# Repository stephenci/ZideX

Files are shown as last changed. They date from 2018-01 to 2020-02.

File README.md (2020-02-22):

# ZideX
Open source 3D printer with dual extrusion and independent X and Z axis
This is a slightly more complicated version of IDEX.
This is also a crane style printer modified to add rigidity to handle fast and rapid movement.

<a href="https://imgur.com/TapHjAb">source: imgur.com</a>

<a href="https://imgur.com/pBOmRLS">source: imgur.com</a>

<a href="https://imgur.com/aCJxu8N">source: imgur.com</a>

<a href="https://imgur.com/a5UugVb">source: imgur.com</a>

<a href="https://imgur.com/xPmkoOy">source: imgur.com</a>

https://youtu.be/PqQjZGIJ1rw

Mostly build documentation and discussion can be found here:
https://openbuilds.com/builds/zidex.5259/

See link below to explore the fully assembled printer in 3D
https://skfb.ly/6vxOx

Full model STEP file posted on Onshape
https://cad.onshape.com/documents/0a614a4674c34d17fad6ca34/w/c56dc46b54dffcec5b4223f7/e/2df415dc5961ccc9e1978c58

license:
CC - Attribution NonCommercial - Share Alike - CC BY NC SA

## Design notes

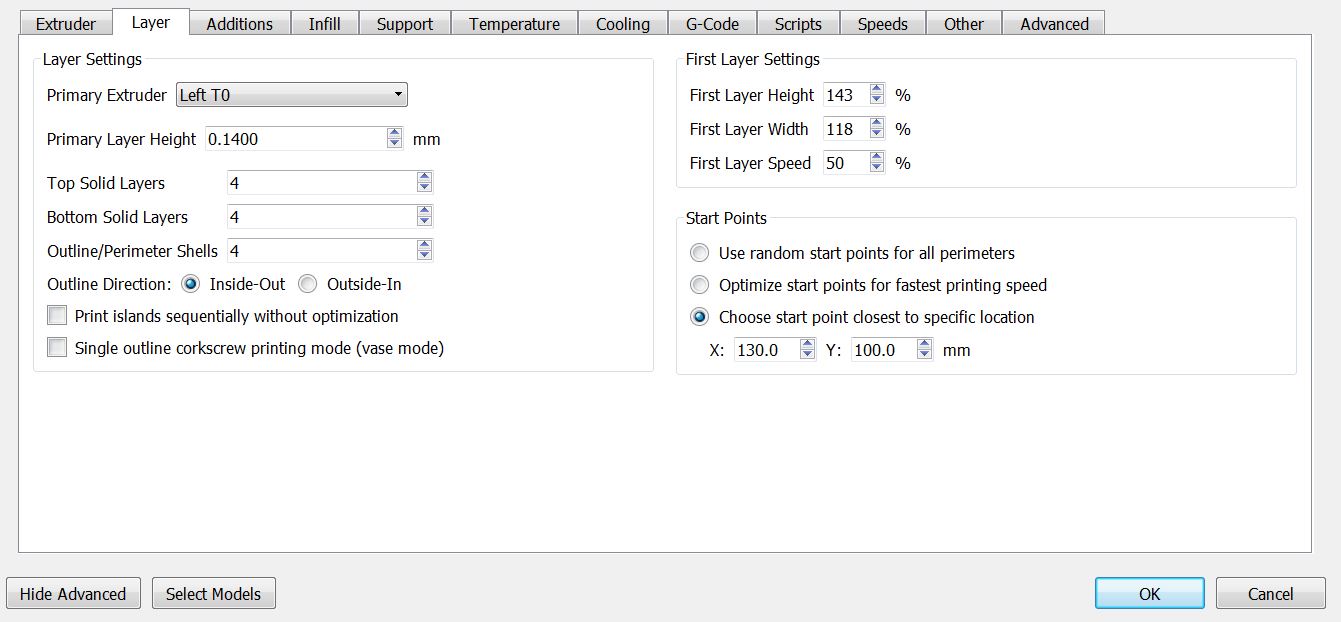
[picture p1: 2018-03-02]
Config/T0 setting (airbrush nozzle) - Layer.JPG

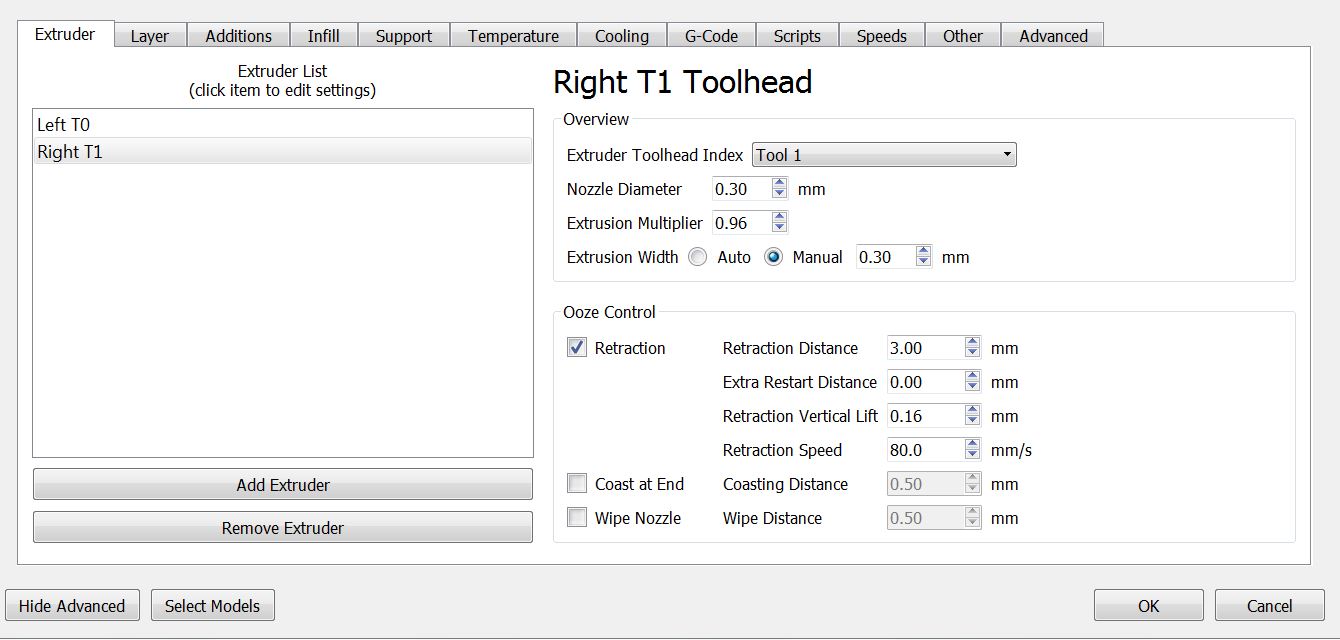
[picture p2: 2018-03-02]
Config/T1 setting (microswiss nozzle) - Extruder.JPG

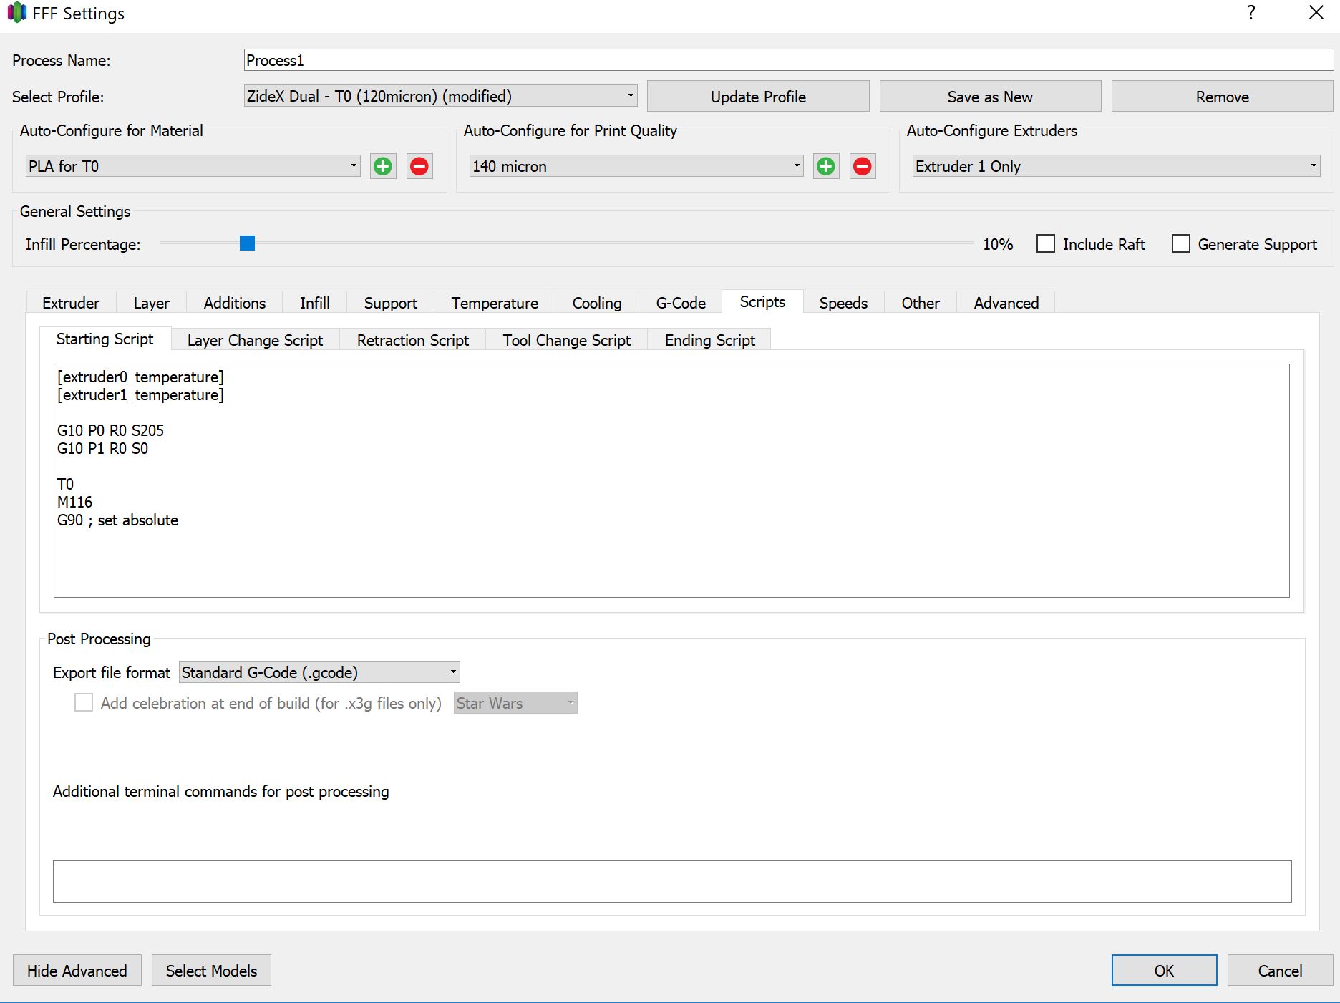
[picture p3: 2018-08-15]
Config/starting script S3D.JPG

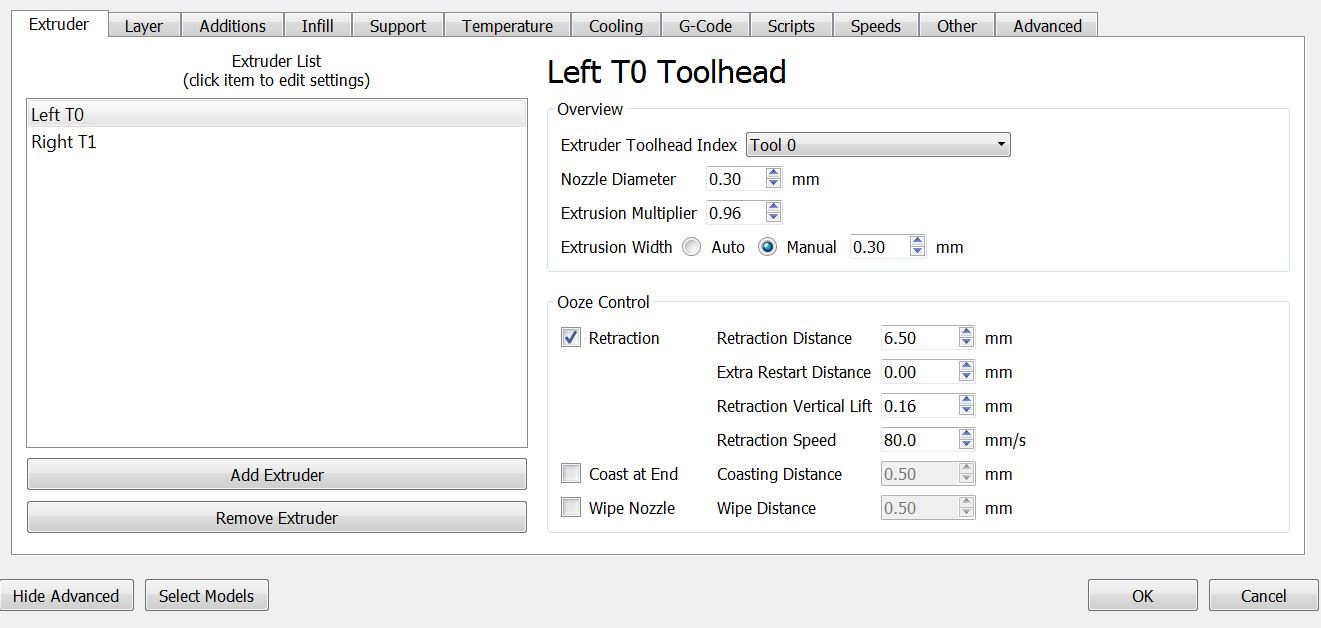
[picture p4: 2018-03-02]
Config/T0 setting (airbrush nozzle) - Extruder.JPG

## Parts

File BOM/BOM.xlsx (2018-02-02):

 |  |  |  | Total | $1337.44
quantity | Hardware | link | $$
2 | Bondtech BMG right hand | https://www.smw3d.com/bondtech-bmg-extruder/ | $160.00
Openbuilds stuff
4 | 20 x 20 x 300 mm | http://openbuildspartstore.com/linear-rail/ | $22.00
3 | 20 x 60 x 350 mm | http://openbuildspartstore.com/linear-rail/ | $26.25
4 | 20 x 40 x 300 mm | http://openbuildspartstore.com/linear-rail/ | $28.60
1 | for Y - C-beam 300 mm | http://openbuildspartstore.com/linear-rail/ | $14.00
1 | for Y - C-beam plate Xlarge | http://openbuildspartstore.com/c-beam-gantry-plate-xlarge/ | $14.95
4 | for Y - V wheel kit | http://openbuildspartstore.com/xtreme-solid-v-wheel-kit/ | $27.00
2 | 6mm - eccentric | http://openbuildspartstore.com/eccentric-spacer/
2 | 6mm - aluminum spacer | http://openbuildspartstore.com/aluminum-spacers/
2 | nema 17 motor mount | http://openbuildspartstore.com/motor-mount-plate-nema-17-stepper-motor/ | $13.90
2 | Tr8*8 375 mm | http://openbuildspartstore.com/8mm-metric-acme-lead-screw/ | $41.50
6 | nema 17 threaded motor mount | http://openbuildspartstore.com/threaded-rod-plate-nema-17-stepper-motor/ | $41.70
4 | mini v gantry kit | http://openbuildspartstore.com/mini-v-gantry-set/ | $123.00
2 | 20 x 80 v slot gantry slot kit w/ extreme wheel | http://openbuildspartstore.com/v-slot-gantry-set/ | $87.10
2 | Z nut block anti backlash | http://openbuildspartstore.com/anti-backlash-nut-block-for-8mm-metric-acme-lead-screw/ | $19.70
2 | 20 x 80 v slot gantry plate only | http://openbuildspartstore.com/v-slot-gantry-plates/ | $24.00
8 | 9mm aluminum spacer | http://openbuildspartstore.com/aluminum-spacers/ | $2.00
4 | v slot gantry spacer | http://openbuildspartstore.com/spacer-block/ | $15.80
4 | Tr8*8 ball bearing | http://openbuildspartstore.com/ball-bearing-688z-8x16x5/ | $4.00
4 | Tr8*8 lock collar | http://openbuildspartstore.com/lock-collar/ | $4.40
3 | pulley kit | http://openbuildspartstore.com/smooth-idler-pulley-wheel-kit/ | $16.35
1 | Y motor pulley 30 teeth | http://openbuildspartstore.com/gt2-2m-timing-pulley-30-tooth/ | $6.95
8 out of 25 | 50 mm | http://openbuildspartstore.com/low-profile-screws-m5/ | $4.85
4 out of 25 | 15 mm | http://openbuildspartstore.com/low-profile-screws-m5/ | $4.85
4 out of 25 | 30 mm | http://openbuildspartstore.com/low-profile-screws-m5/ | $4.85
10 | self tapping screw for Z tower | http://openbuildspartstore.com/self-tapping-screw/ | $2.50
1 | 24 v meanwell power supply 30mm | http://openbuildspartstore.com/24v-14-6a-meanwell-power-supply/ | $50.00
4 | 20mm spacer | http://openbuildspartstore.com/aluminum-spacers/ | $1.40
20 | 1mm thick precision shim | http://openbuildspartstore.com/precision-shim-10x5x1mm/ | $5.00
5 out of 10 | micro limit switch | Aliexpress | $1.14
30 out of 50 | angle connector | Aliexpress | $12.26
4 out of 5 | Zs and Xs motor pulley 20 teeth | Aliexpress | $3.33
5 | Nema 17 1.8 deg, 40mm, 2A rated | Amazon - stepperonline | $58.00
2 | Nema 17 pancake 0.9 deg, 20mm, 1.2A | http://www.ebay.com/itm/US-Ship-0-9deg-Nema-17-Stepper-Motor-Bipolar-1-2A-15-6oz-in-42x42x20mm-4-wires-/331601550528 | $19.40
 | 1164 Gates genuine GT3 belt 2mm pitch | http://www.royalsupply.com/store/pc/viewCategories.asp?idCategory=4609 | $30.00
2 | 168 mm loop GT3 belt 2mm pitch | http://www.royalsupply.com/store/pc/viewCategories.asp?idCategory=4609 | $5.20
2 | screw Pulley for Z 40 teeth | https://www.robotdigg.com/product/146/GT2-40-Tooth-8mm-Bore-Pulley | $7.00
1 | duet wifi | https://www.filastruder.com/collections/electronics | $170.00
1 | duex 2 drive expansion board | https://www.filastruder.com/collections/electronics | $75.00
2 | E3D V6 for bowden kit | https://www.filastruder.com/collections/e3d-hotends/products/all-metal-e3d-v6-hotend?variant=1236046392 | $150.00
12 | MR83ZZ | Aliexpress
1 | Corneria 10 Magnetic Sheets Adhesive 20 Mil Magnet | Amazon - Corneria | $10.46
1 | Geckotek RT 120x120mm | https://www.geckotek.co/product/geckotek-rt-build-plate-3d-printing-surface/ | $29.00

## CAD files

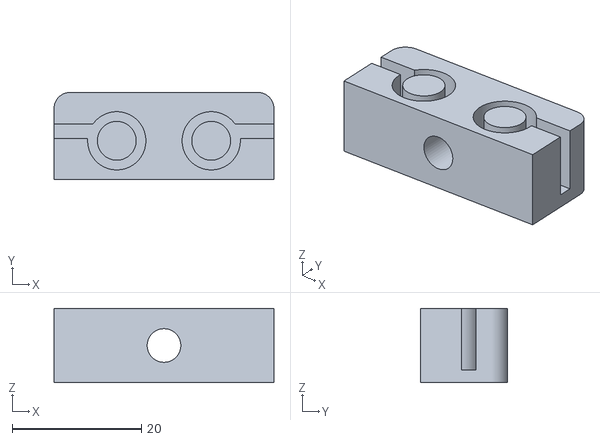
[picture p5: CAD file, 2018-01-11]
STL/Y3 - credit Mark R.stl
34.0 x 13.5 x 11.5

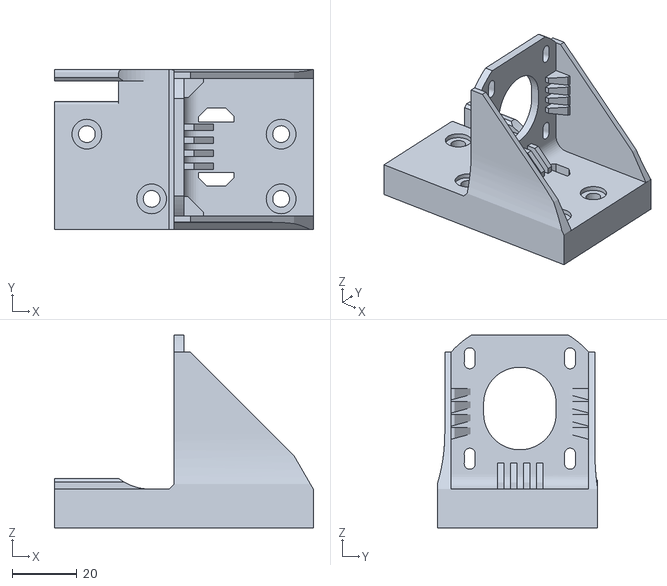
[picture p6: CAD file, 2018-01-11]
STL/Y1.stl
80.0 x 49.5 x 59.5

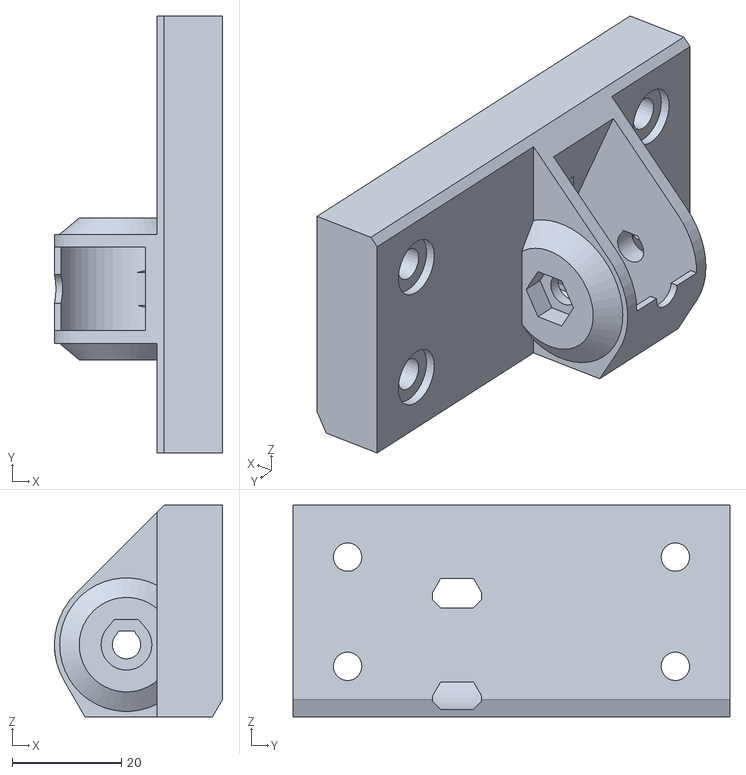
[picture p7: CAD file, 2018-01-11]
STL/Y2 - credit IndieI2.stl
30.8 x 80.0 x 38.7

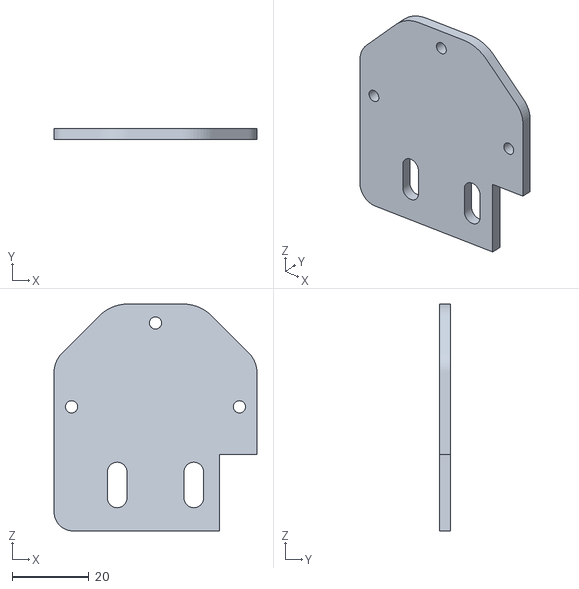
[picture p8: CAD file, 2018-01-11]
STL/X6a - Copy of X6.stl
53.0 x 3.00 x 59.3

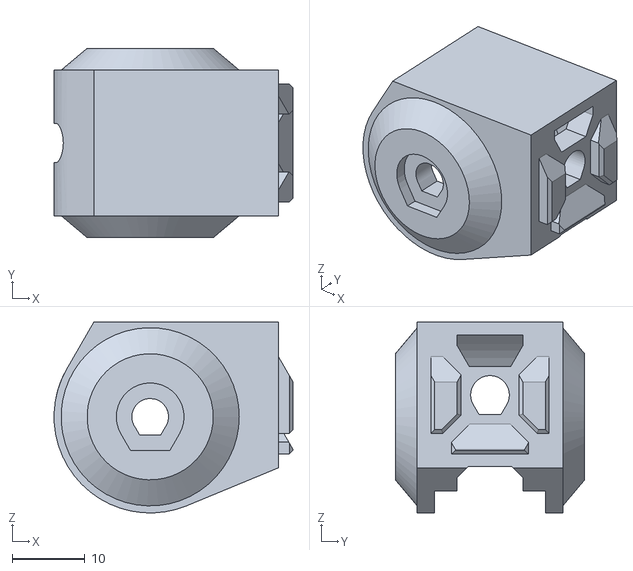
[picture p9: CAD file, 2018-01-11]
STL/X5 - credit to IndieI2.stl
32.8 x 26.0 x 26.2

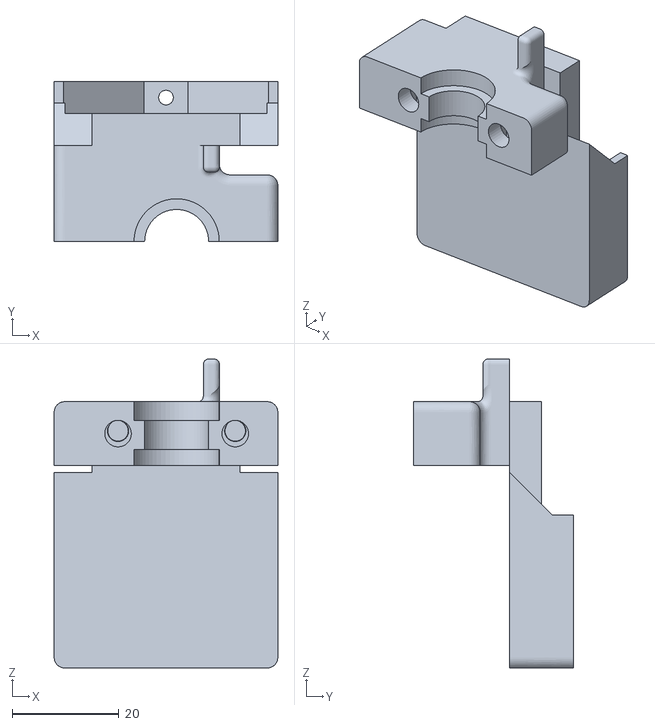
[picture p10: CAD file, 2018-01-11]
STL/X2.stl
42.0 x 30.0 x 58.0

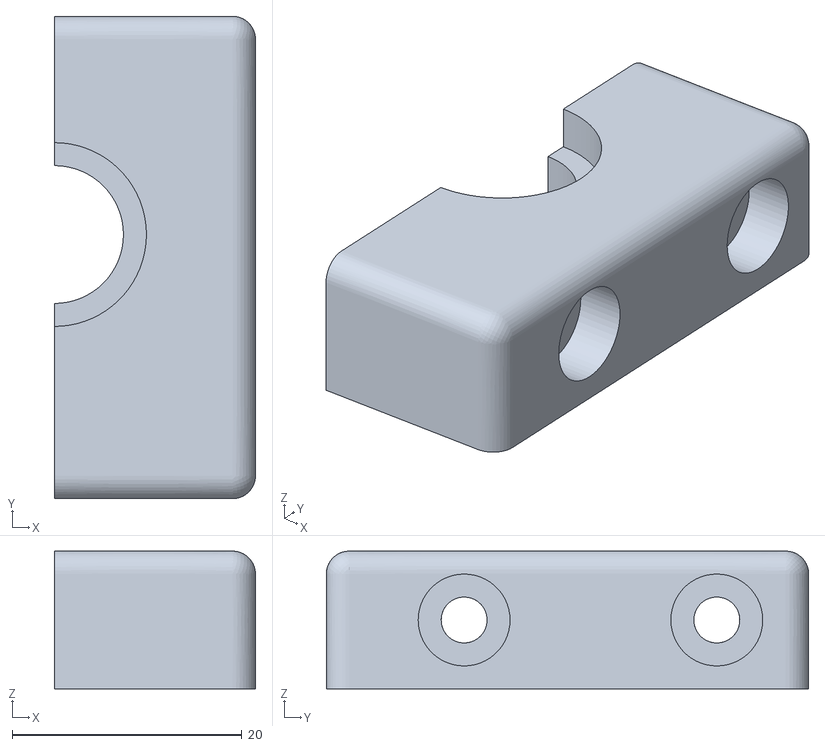
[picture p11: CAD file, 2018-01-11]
STL/X3.stl
17.5 x 42.0 x 12.0

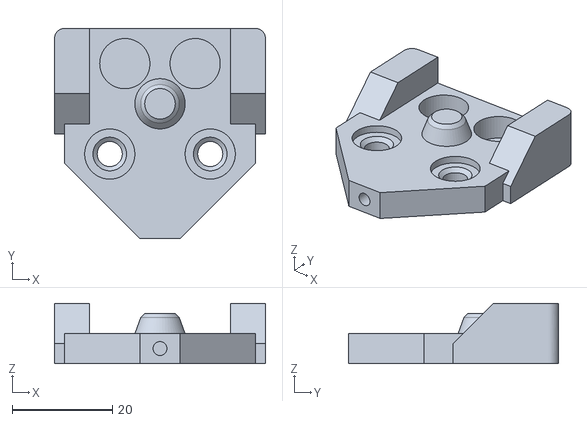
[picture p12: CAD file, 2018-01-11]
STL/X1.stl
42.0 x 41.8 x 12.0

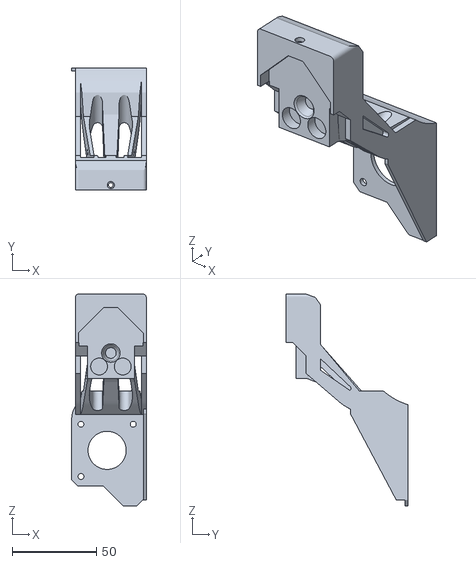
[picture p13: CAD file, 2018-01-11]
STL/X4.stl
44.3 x 72.5 x 125.7

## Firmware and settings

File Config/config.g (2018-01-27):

; Configuration file for Duet WiFi (firmware version 1.17)
; executed by the firmware on start-up
;
; generated by RepRapFirmware Configuration Tool on Mon Sep 18 2017 23:51:32 GMT-0700 (Pacific Daylight Time)

; General preferences
M111 S0 ; Debugging off
G21 ; Work in millimetres
G90 ; Send absolute coordinates...
M83 ; ...but relative extruder moves
M555 P1 ; Set firmware compatibility to look like RepRapFirmare
M584 X0 Y1 U6 Z2:5 E3:4
M208 X-8 U-8 Y-7 Z0 S1 ; Set axis minima
M208 X127 U127 Y166 Z127 S0 ; Set axis maxima

; Endstops
M574 Z0 S0 ; Define active low and unused microswitches
M574 X1 U1 Y1 S1 ; Define active high microswitches
M558 P6 X0 Y0 Z1 H132 F120 T12000 ; Set Z probe type to unmodulated, the axes for which it is used and the probe + travel speeds
G31 P600 X0 Y0 Z0.26 ; Set Z probe trigger value, offset and trigger height basically the thickness of FSR
;M557 X5:120 Y5:120 S15 ; Define mesh grid

; Drives
M569 P0 S0 ; Drive 0 goes forwards X
M569 P1 S0 ; Drive 1 goes forwards Y
M569 P2 S1 ; Drive 2 goes forwards Z
M569 P3 S0 ; Drive 3 goes forwards extruder T0
M569 P4 S0 ; Drive 4 goes forwards extruder T1
M569 P5 S1 ; Drive 5 goes forwards Uz
M569 P6 S1 ; Drive 6 goes forwards Ux
M350 X16 U16 Y16 Z16 E16:16 I1 ; Configure microstepping with interpolation
M92 X80 U80 Y53.33 Z800 E830:415 ; Set steps per mm
M566 X1200 U1200 Y1200 Z60 E1200:1200 ; Set maximum instantaneous speed changes (mm/min)
M203 X15000 U15000 Y15000 Z180 E6000:6000 ; Set maximum speeds (mm/min)
M201 X2500 U2500 Y1500 Z250 E1000:1000 ; Set accelerations (mm/s^2)
M906 X950 U950 Y950 Z980 E800:800 I60 ; Set motor currents (mA) and motor idle factor in per cent
M84 S30 ; Set idle timeout

; Heaters
M143 S260 ; Set maximum heater temperature to 260C
M140 H-1 ; Disable heated bed
M305 P1 T100000 B4725 C7.06e-8 R4700 ; Set thermistor + ADC parameters for heater 1
M305 P2 T100000 B4725 C7.06e-8 R4700 ; Set thermistor + ADC parameters for heater 2
M307 H1 A535.7 C135.1 D2.6 B0 S0.8
M307 H2 A535.7 C135.1 D2.6 B0 S0.8

; Tools
M563 P0 D0 H1 ; Define tool 0 default Fan0
G10 P0 X0 Y0 Z0 ; Set tool 0 axis offsets
G10 P0 R0 S0 ; Set initial tool 0 active 0c and standby temperatures to 0C
M563 P1 D1 H2 X3 F1; Define tool 1 use Fan1
G10 P1 Y-40.45 U4.8 Z0 ; Set tool 1 axis offsets
G10 P1 R0 S0 ; Set initial tool 1 active 0c and standby temperatures to 0C

; Network
M550 Pzidex ; Set machine name
M551 Pzidexwifi ; Set password
M552 S1 ; Enable network

M586 P0 S1 ; Enable HTTP
M586 P1 S0 ; Disable FTP
M586 P2 S0 ; Disable Telnet

; Fans
M106 P0 H-1 ; Set fan 0 Thermostatic control is turned off
M106 P1 H-1 ; Set fan 1 Thermostatic control is turned off
M106 P3 T45 H1 ; Set fan 3 on when hotend 45c .Thermostatic control is turned on for heater 1
M106 P4 T45 H2 ; Set fan 4 on when hotend 45c .Thermostatic control is turned on for heater 2
;M106 P2 S1 I0 F500 H1:2 T45 ; Set fan 2 value, PWM signal inversion and frequency. Thermostatic control is turned on

; Custom settings are not configured

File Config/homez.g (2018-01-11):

; homez.g
; called to home the Z axis
;
; generated by RepRapFirmware Configuration Tool on Mon Sep 18 2017 23:51:32 GMT-0700 (Pacific Daylight Time)

; Lift Z relatively to current position
;G91
;G1 Z5 F12000

; Back to absolute positioning
M0
G90
G92 Z0 ; Momentarily set Z to 0 position so tool change can be executed

M584 Z2 ; Split the 2 Z towers for independent control. this will move left tower only
T0 P0 ; Select Tool 0 without running tfree tpre tpost
G1 X59 Y59 F12000 ; T0 Go to center bed probe point 
G30 ; this will home and probe the left Z tower
; lift left Z tower after probing
G91
G1 Z5 F200
G90
T1 P1 ; Select Tool 1 and run tfree0 only to park T0

M584 Z5 ; Split the 2 Z towers for independent control. this will move right tower only
G1 X59 Y59 F12000 ; T1 Go to center bed probe point
M558 P6 X0 Y0 Z1 H132 F120 T12000 ; Allow right tower to go all the way down to FSR on bed
G30 ; this will home and probe the right Z tower
; lift right Z tower after probing
G91
G1 Z5 F200
G90
T0 P1 ; Select Tool 0 and run tfree1 only to park T1


M584 Z2:5 ; join both Z together
M558 P6 X0 Y0 Z1 H132 F120 T12000

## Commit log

2018-01-11 Add files via upload
    All STLs related to X axis and U axis
    [X1.stl, X1a - Copy of X1.stl, X2.stl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]
2018-01-11 Add files via upload
    all STLs for Y axis
    [Y1.stl, Y2 - credit IndieI2.stl, Y3 - credit Mark R.stl]
2018-01-11 Rename Description to All STL here
2018-01-11 Update and rename Lists to config.g
    [config.g]
2018-02-02 Added Geckotek plate and magnet sheet
    [BOM.xlsx]
2018-03-02 For simplify 3D additional toolhead setting dual
